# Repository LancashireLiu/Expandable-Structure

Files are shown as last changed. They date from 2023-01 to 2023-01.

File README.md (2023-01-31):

# 可展多面体机构

这个项目是未来技术学院本科二年级设计与建造Ⅱ课程的课程设计，我是本项目的组长。下面Readme文档简要介绍了本项目的过程，上方repository库中包含了项目的全过程以及报告等内容！

天津大学可动结构实验室的马家耀教授[个人主页](http://motionstructures.tju.edu.cn/ch/team/majiayao.html)为本项目的导师。

***

可展多面体机构是一种在实现其承载功能的前提下，能够大尺寸地改变几何形状与空间构型的结构。

可展多面积机构可以适应不同的应用需求，是空间可折展结构和大型可折展设备的关键技术。

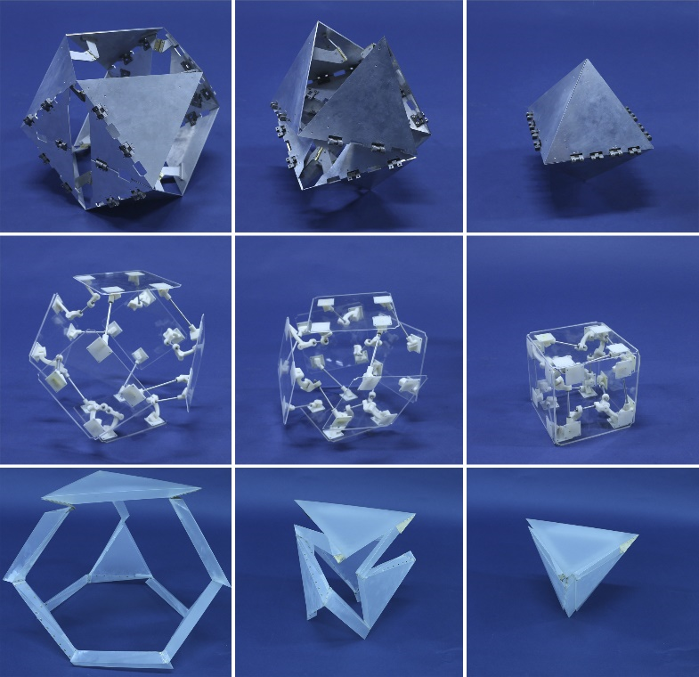
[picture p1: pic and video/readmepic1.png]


单自由度可展多面体机构可以实现单一驱动下两个空间构型的切换，如上图中截角八面体和立方体之间的变换，在展开时可大幅增加工作空间与面积，在完全折叠状态下可减少储存和运输空间。对多面体展开与折叠构型进行分析，确定各顶点的运动副类型及方位，用以形成具有协调运动的多面体空间机构网格。

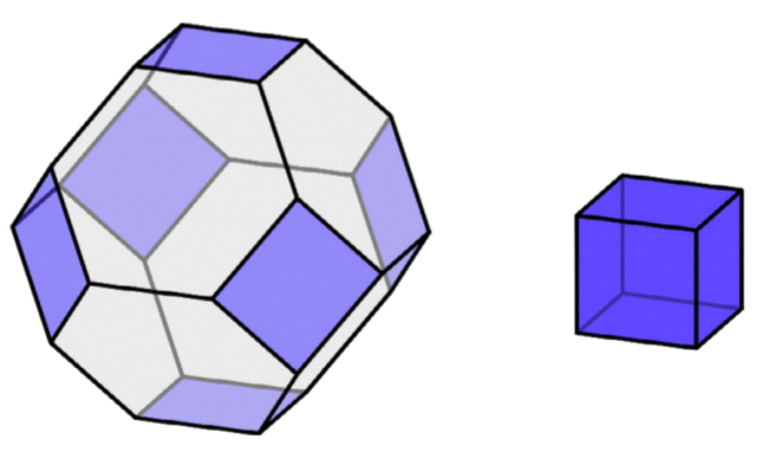
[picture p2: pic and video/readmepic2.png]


上图中中层的截角八面体和立方体之间的可展结构就是我们的项目。

为了保证机构在空间中运动是保持单自由度的，多面体每个连杆和正方形表面之间的连接转轴（称为转动副）需要是确定的。这种连杆机构称为Bricard机构，通过空间几何性质可以计算出这些转轴（转动副）和完全活动的顶点（称为球副）的空间坐标和角度。

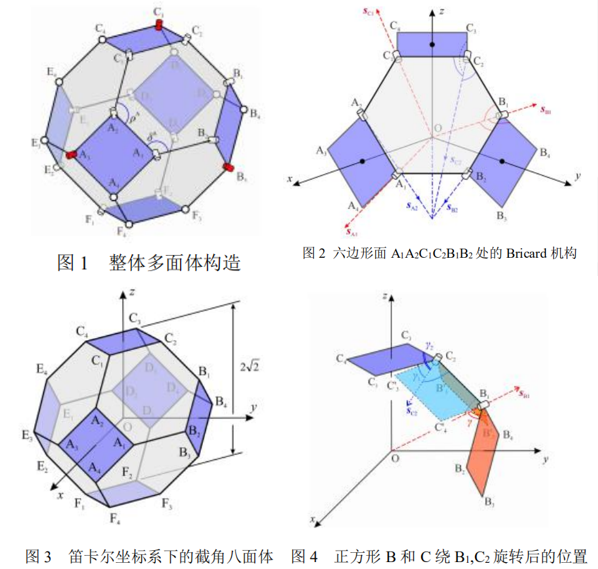
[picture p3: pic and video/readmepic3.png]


> 机构初始状态为一截角八面体，其整体构造如图 1 所示。本机构以三重对称 Bricard 连杆机构为折展运动单元，采用 15 个转动副与 9 个球副。经计算，该可 展机构的自由度为 1。Bricard 机构如图 2 所示。原点的定义及坐标系的建立如图 3 所示。正方形 B 围绕 B1 关节轴线旋转，正方形 C 围绕 C2关节旋转，使 B4与 C2重合，C1 与 B1 重合（如图 4 所示），由于 Bricard 机构的三重对称性以及六 边形 D1D2E1E2F1F2与六边形A1A2C1C2B1B2结构相同，因此可得出其他点的运动 过程。其运动顺序如图 4 所示。

可展机构

通过立体几何矩阵理论可以计算出所有结点在空间中的位置和转轴（转动副）的朝向向量。

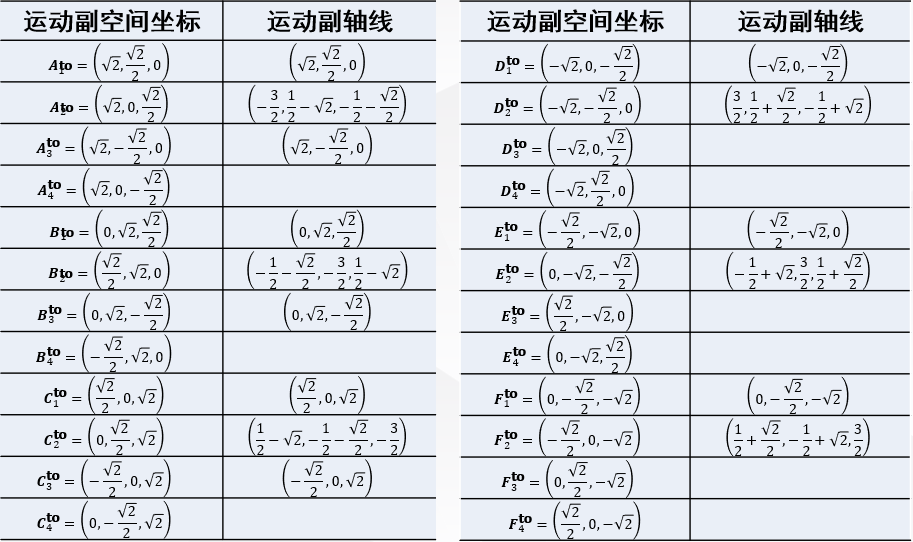
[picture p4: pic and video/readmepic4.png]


之后用Solidworks进行建模，首先建立三个面的Bricard结构，然后用两个相同的Bricard结构拼接成最后的模型。

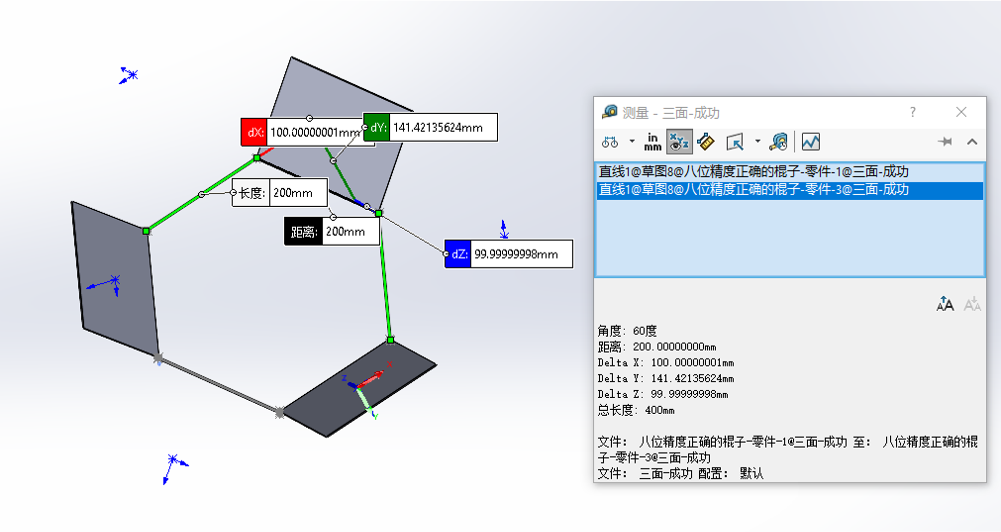
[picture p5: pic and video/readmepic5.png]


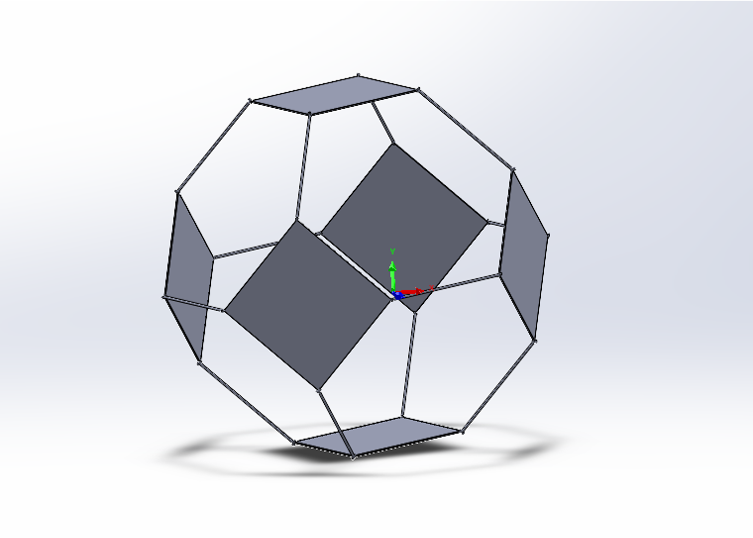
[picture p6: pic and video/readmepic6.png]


[运动学建模视频](https://github.com/LancashireLiu/Expandable-Structure/blob/main/pic%20and%20video/video1.mp4)

进行零件、静态和动力学建模后，我确定了实物大小，实物材料（表面使用亚克力板，转动副和球副3d打印，连杆不锈钢），使用建模出的数据打印和制作，拼装后得到实物。

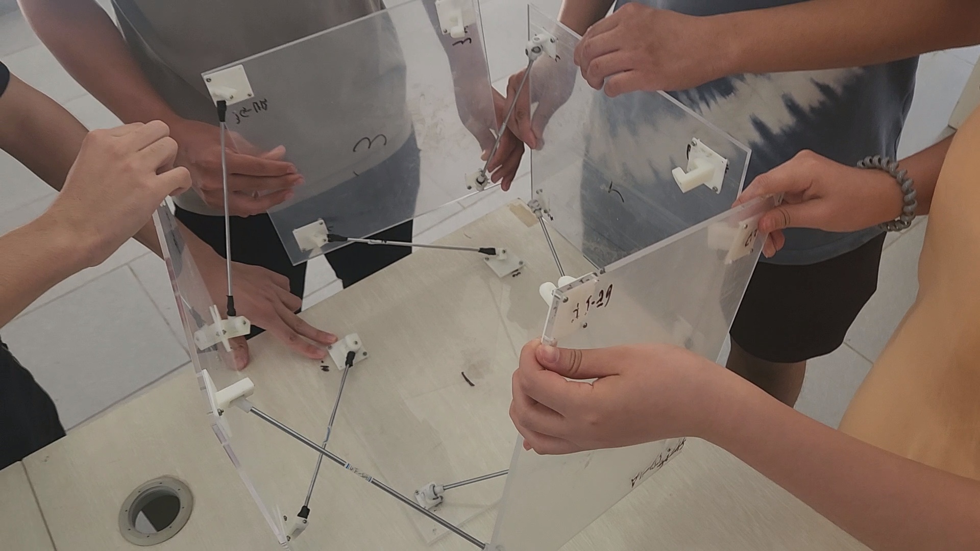
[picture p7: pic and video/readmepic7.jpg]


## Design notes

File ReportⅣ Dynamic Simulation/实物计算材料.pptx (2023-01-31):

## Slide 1

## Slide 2

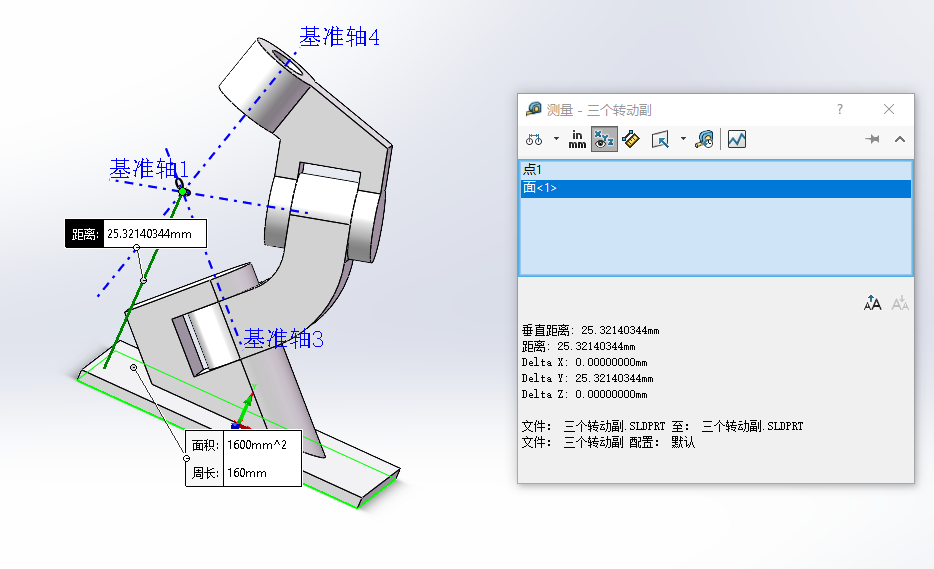
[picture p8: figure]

- H=2.53cm

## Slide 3

可展结构——运动学仿真分析

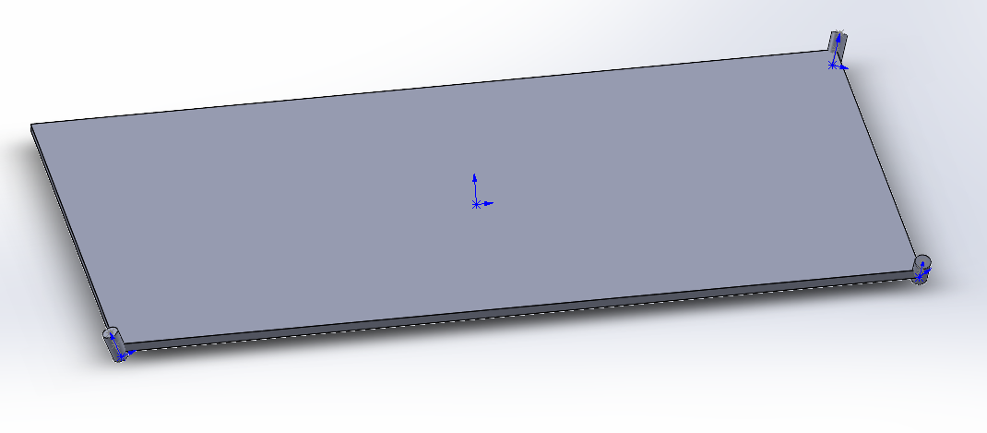
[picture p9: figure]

Ⅱ类转动副
与C1C4、C1C2夹角：108.43494882°、 108.43494882°

C3

C4

C2

C1

Ⅱ类转动副
与C2C1、C2C3夹角： 95.57617619°
134.72950752°

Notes: 两个转动副扭角：34.78648675°，和连杆的情况一样，接下来只需要拼接即可

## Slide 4

- 转动副Ⅰ
- h=1.98cm

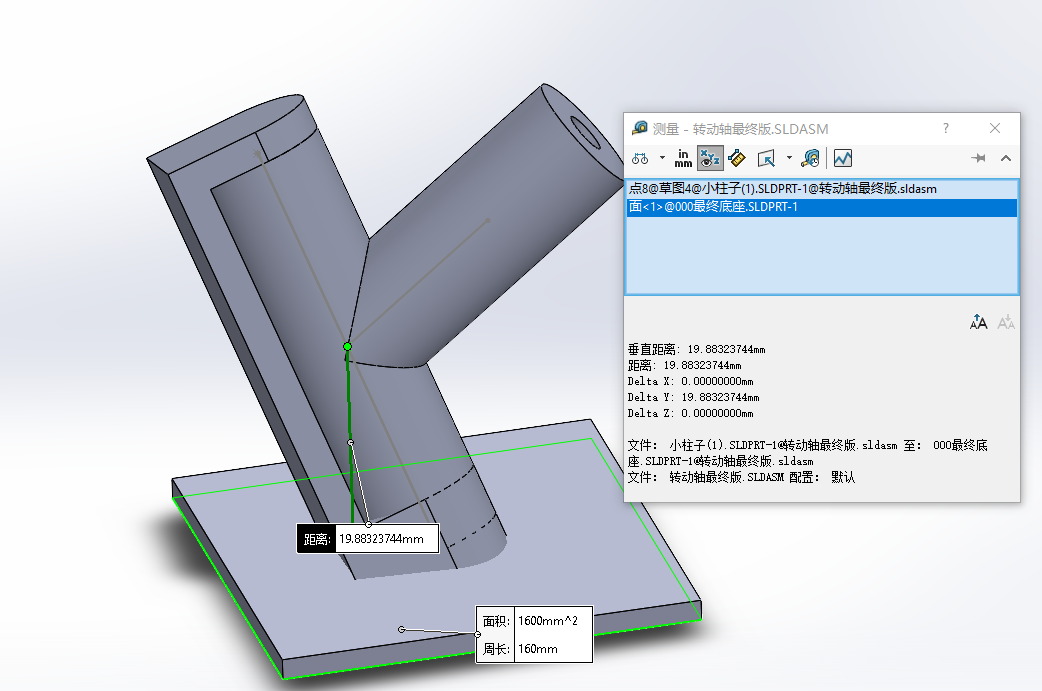
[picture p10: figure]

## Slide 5

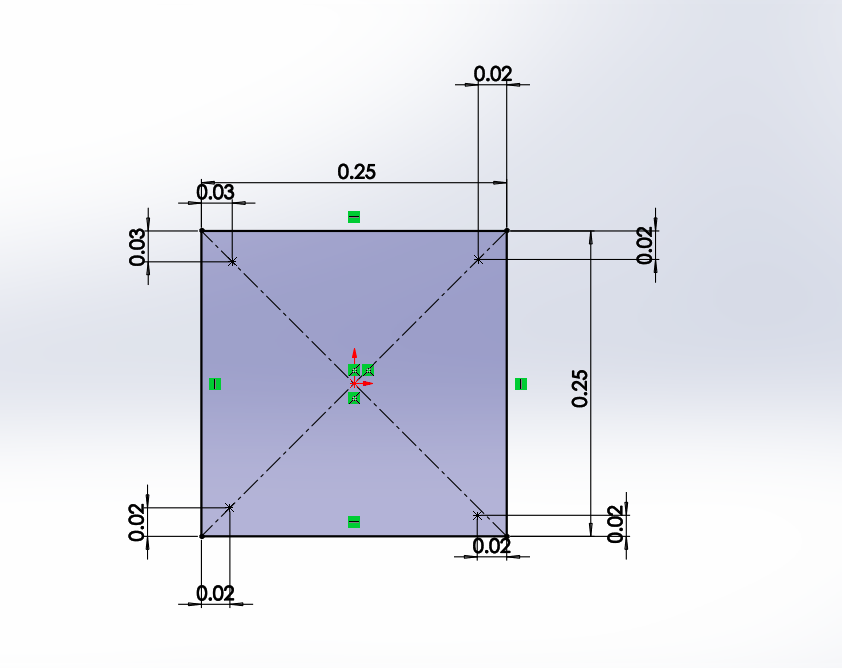
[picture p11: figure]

2.53cm

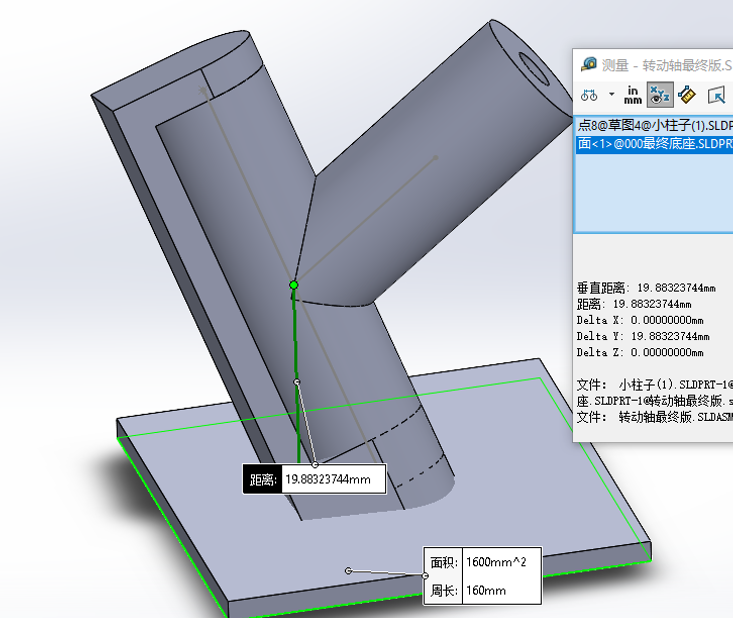
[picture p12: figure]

2.34cm

1.73cm

2.34cm

2.42cm

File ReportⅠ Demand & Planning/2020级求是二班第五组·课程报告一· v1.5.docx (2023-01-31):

课程报告1 项目计划

1.1 可展结构资料综述

可展机构在航空航天、建筑、汽车、消防等领域都有着广泛的应用，是人类用以传递力的重要机构。随着全球工业化的快速发展，机械基本上取代了传统的手工的发展，而可展机构为人类生活生产提供了不可忽视的便利性，在航天航空、日常生活, 机器人等领域应用广泛。因此这种机构的机械设计和运动分析研究得到国内研究机构的普遍重视。但对于不同可展机构的开发与应用, 还需要更多针对性的研究与探索。

可展结构的具有众多优秀特性。

（1）结构紧凑、尺寸小巧，且设备收缩后体积小。这是可展机构最大的优点，也使得其作业所要求的占用空间小。在地下水位较高的地区工作时对机坑的处理会十分简单。它能够在任何已有设备上直接使用，而无需修改设备结构和机坑深度。

（2）载荷能力大、稳定性好。相对于其他机构来讲，大部分可展机构的承载能力偏大。由于其稳定的结构，可展机构在额定承载能力和伸展长度下，具有很好的稳定性。

（3）定位精准。大部分可展机构在运行过程能确保在行程的任意一点精确定位，并锁定高度，不像液压设备会因温度的变化或泄漏产生位置变化。

（4）运行平稳、噪音较低。由于其连续成型原理，无垂直方向爬行，使得机构运转平稳安静，除驱动装置的运行噪音，大部分可展器本身的工作噪音很低。

（5）效率高。大部分可展设备的总传动效率较高，通常可达到 80%以上。

（6）构造简单，使用方便。可展机构的结构精巧而简洁，所以可展器本身的安装工作简易而快捷，一块伸缩机构通常在很短的时间即可安装使用。

（7）通用性高。可展机构对使用环境没有太高要求，使其经常在太空、海洋等复杂环境下工作，并依然保持其稳定性。

我们所需要的完成的截角八面体 (由八个六边形和六个四边形围成的十四面体)的体积折展比分别为11.3，可在展开状态下可显著提升工作空间。这些多面体变换过程无运动分叉现象, 具有结构简单和易于控制等特点。通过桁架变换方法，构件可在保持单自由度变换特点的同时降低机构的过约束度数, 从而以较低过约束度甚至非过约束的机构实现变换，减少因过约束带来的制造和装配的苛刻要求，也避免了因构件变形而产生的机构锁死现象，增强了应用的可行性。

1.2 工程师职责

（1）注重产品质量，控制好产品研发进度。

（2）协调各方面工作，确保工作顺利进行。

（3）每周完成组内分配的任务，认真执行计划，按时汇报自己的工作，不因为个人原因拖慢组内进度。

（4）端正工作态度，严谨认真，刻苦钻研，脚踏实地，讲求效率。

（5）正确认识自我，遇到问题及早提出。

1.3 项目管理

项目进度安排甘特图如图1-1 。

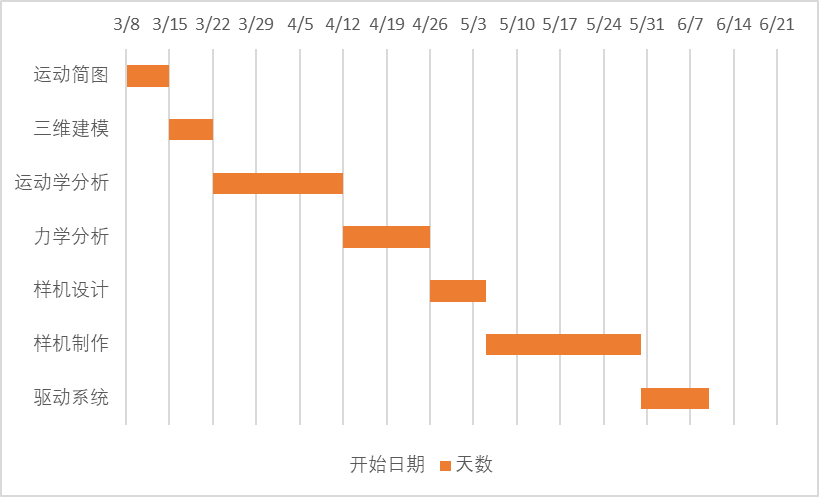
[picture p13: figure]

图1-1 项目进度安排甘特图

成员分工安排如下：

刘宇轩：组长，负责主管项目进程，组员的任务分配及监督各项任务的完成情况。在具体工作上，负责可展多面体运动简图的描画，三维建模过程，运动学过程分析，力学过程分析，样机设计及制作。

张佳瑜：负责可展多面体运动简图的描画，运动学过程分析，力学过程分析，样机设计及制作。

罗松寒：负责可展多面体运动简图的描画，三维建模过程，运动学过程分析，力学过程分析，样机制作。

白韬：负责可展多面体运动简图的描画，运动学过程分析，力学过程分析，样机制作，可展多面体驱动系统，。

郭伟祺：负责可展多面体运动简图的描画，三维建模过程，运动学过程分析，力学过程分析，样机制作。

冒惠敏：负责可展多面体运动简图的描画，运动学过程分析，力学过程分析，样机设计与制作。

1.4 项目任务书

项目题目——可展机构

1.4.1 用途及功能要求

可展多面体机构在实现其承载功能的前提下，能够大尺寸地改变几何形状与空间构型，以适应不同的应用需求，是空间可折展结构和大型可折展设备的关键技术。单自由度可展多面体机构可以实现单一驱动下两个空间构型的切换，如图一中截角八面体和立方体之间的变换，在展开时可大幅增加工作空间与面积，在完全折叠状态下可减少储存和运输空间。对多面体展开与折叠构型进行分析，确定各顶点的运动副类型及方位，用以形成具有协调运动的多面体空间机构网格。图1-2展示了截角八面体和立方体之间的变换。


图1-2 截角八面体和立方体之间的变换

1.4.2 设计要求和原始数据

（1）设计一种可在截角八面体与立方体之间变换的可展多面体机构；

（2）可展多面体折叠构型下立方体边长200-300mm，机构自由度≤2；

（3）可展多面体折展过程中需避免因零件碰撞而产生的物理干涉；

（4）可展多面体在完全展开状态需保证构型的稳定性。

设计原始数据如下：

表1-1 设计原始数据

方 案 号 | 1－1 | 1－2 | 1－3 | 1－4
整体自由度数 | 1 | 2 | 1 | 2
折叠构型下立方体边长a/mm | 200 | 200 | 300 | 300

1.4.3 设计内容

（1）确定可展多面体折展前后的顶点坐标及多边形单元的基本尺寸；

（2）选定可展多面体顶点处运动副形式，计算转动副空间轴线位置，设计转动副的物理实现形式；

（3）设计合理的零件外形及具体尺寸并确定各类零件数量，避免物理干涉；

（4）设计锁死装置保证可展多面体具有稳定展开构型。

1.4.4 提交的设计结果

（1）可展多面体的机构运动简图，包括顶点处运动副类型，以及转动副空间方位；

（2）可展多面体三维软件建模模型，需包含运动模拟中的3-4个典型折展状态；

（3）可展多面体典型顶点运动轨迹；

（4）可展多面体静力学分析；

（5）各类零件尺寸图若干张；

（6）原理样机；

（7）设计计算说明书，内容包括：

* 设计流程和设计原始数据；

* 可展多面体顶点坐标与各个顶点处转动副的具体轴线方位计算；

* 可展多面体三维建模的过程说明；

* 零件外形及具体尺寸的设计文本。

1.4.5 评价指标及标准

（1）尺寸小、自由度少、体积折展大；

（2）原理样机具有较为规则平整的外观构型；

（3）原理样机能够在最大与最小构型之间折展，且折展过程流畅；

（4）原理样机在完全展开状态应具有较高的稳定性和承载力。

1.5 项目需求分析

表1-2展示了可展多面体的项目需求分析。

表1-2 项目需求分析

需求分析 | 需求表达
机构设计需求 | ① 可展机构 ② 结构体系 ③ 驱动源
用户情况 | 1 面向用户对象 2 使用场合、领域
作品效益 | 1 社会效益及经济效益 2 时间消耗及产出 3 使用频率 4 资金消耗及回报 5 信息使用价值

1.6 产品规格

1.产品体积：可展多面体折叠构型下立方体边长200-300mm，体积大小为8000cm³-27000cm³。

2.产品结构：本机构以三重对称 Bricard 连杆机构为折展运动单元，采用 15 个转动副与 9 个球副。

3.自由度：机构自由度≤2。

4.驱动源:

（1）微电机驱动

在结构上分散或集中布置微电机，直接驱动主动件或通过传动使机构展开或折叠。

（2）弹簧(扭簧、拉簧)元件驱动

在机构节点或杆件中点处按特定要求设詈弹簧元件，折叠时弹簧受预应力存贮弹性变性能；当机构解锁后，弹簧释放弹性能，驱动机构协调同步展开。

（3）自伸展驱动

结构的一部分构件、某些特定构件的中点、整个结构元件，由记忆合金、自适应智能元件等构成，使其在特定环境下可按设计要求自动展开。

5.自锁方式:

（1）有限自锁

在摇杆末端设置一个小凹槽，凹槽位置在转动结束后所在的角度上。在固定 处固定一个细短杆，转动结束后细短杆刚好接到凹槽里。或者在两面之间添加一 个伸缩杆，伸缩杆通过类似装置实现自锁（类比雨伞），从而实现两面高度之间的自锁。

优点：旋转结束后，自锁较稳定。

缺点：回复原六面体有不确定因素。

（2）棘轮自锁

在某一转动副处进行改装，安装一个棘轮。保证转动副只按照特定轨迹单向转动，从而保证在展开的各个阶段都能得到较好的稳定性。此外通过对棘轮的解放，实现由截角八面体到六面体的转换。或者在两个面之间安装连杆装置，通过棘轮实现自锁。

优点：稳定度高，不确定因素少。

缺点：装置复杂，制作过程困难。

（3）涡轮涡杆自锁

在两面之间安装涡轮涡杆结构，通过设计螺旋角和摩擦系数实现自锁。

优点：稳定度高，不确定因素少。

缺点：计算量大，装置复杂。

表1.3展示了项目作品的规格参数表。

表1.3 产品规格参数表

产品规格参数表
产品构件组成 | 零件类型 | 方形面板 | 铰链底座 | 直杆1 | 直杆2 | 直杆3
| 数量(个） | 6 | 24 | 6 | 6 | 3
| 零件类型 | 弯杆1 | 弯杆2 | 螺栓 | 轴承 | 圆柱销
| 数量（个） | 9 | 9 | 96 | 18 | 30
产品数据参数 | 立方体边长 | 自由度 | 驱动源 | 自锁方式 | 折展比 | 折展解构单元
| 280mm | 1 | 微电机 | 棘轮自锁 | 11.314 | 三重对称Bricard连杆机构

1.7 产品概念选择

六步骤选择项目作品概念

步骤一：准备选择矩阵

作品概念评分矩阵表如表1.4

表1.4 概念评分矩阵表

作品概念
选择标准 | 权重 | 自锁方式 | | | | | | 驱动方式
| | 有限自锁 | | 棘轮自锁 | | 涡轮涡杆自锁 | | 微电机驱动 | | 弹簧驱动
| | 评分 | 加权分 | 评分 | 加权分 | 评分 | 加权分 | 评分 | 加权分 | 评分 | 加权分
精确度 | 25% | 3 | 0.075 | 4 | 0.1 | 4 | 0.1 | 4 | 0.1 | 3 | 0.075
稳定性 | 20% | 4 | 0.08 | 5 | 0.1 | 4 | 0.08 | 4 | 0.08 | 3 | 0.06
流畅度 | 15% | 4 | 0.06 | 4 | 0.06 | 5 | 0.075 | 4 | 0.06 | 3 | 0.045
可恢复性 | 10% | 2 | 0.02 | 4 | 0.04 | 4 | 0.04 | 3 | 0.03 | 1 | 0.01
资金预算 | 10% | 5 | 0.05 | 3 | 0.03 | 2 | 0.02 | 2 | 0.02 | 3 | 0.03
计算量 | 10% | 3 | 0.03 | 4 | 0.04 | 2 | 0.02 | 2 | 0.02 | 2 | 0.02
组装难易 | 5% | 4 | 0.02 | 2 | 0.01 | 3 | 0.03 | 2 | 0.01 | 2 | 0.01
整体重量 | 5% | 5 | 0.025 | 4 | 0.02 | 3 | 0.015 | 2 | 0.01 | 4 | 0.02
总评 | 100% | 0.36 | | 0.4 | | 0.38 | | 0.33 | | 0.27
是否采用 | | 否 | | 是 | | 否 | | 是 | | 否

步骤二：作品概念评估

以所有标准，对一个概念评估，然后转向下一个概念。

选择标准：精确度、稳定性、流畅度、可恢复性、资金预算、计算量、组装难易、整体重量。

步骤三：作品概念排序

自锁方式：1.棘轮自锁 2.涡轮涡杆自锁 3.有限自锁

驱动方式：1.微电机驱动 2.弹簧驱动

步骤四：作品概念组合与改进

对作品概念进行组合，保持优势，减少劣势。

步骤五：选出一个作品概念

选择结果：棘轮自锁、微电机驱动

步骤六：反思结果与过程

检查选出的作品概念，确保每位成员满意。

1.8 产品目标指标

1.尺寸：可展多面体折叠构型下立方体边长280mm。

2.自由度：可展机构的自由度为1。

3.驱动源：经过项目作品概念评估矩阵表加权之后权重最高的驱动方式，经评定为微电机驱动的方式。

4.自锁方式：经过项目作品概念评估矩阵表加权之后权重最高的自锁方式，经评定为棘轮自锁的方式。

表1.5展示了项目作品的最终指标。

表1.5 产品最终指标

选择标准 | 指标要求
精确度 | 自锁角度误差小于3%
稳定性 | 展开结构承重极限≥500g
流畅度 | 响应时间≤0.1秒
可恢复性 | 恢复时间≤3秒
产品大小 | 立方体边长≤280mm

1.9 运动副坐标及轴线计算结果

表1.6展示了可展多面体的运动副和运动副轴线的计算结果。详细的计算过程在本报告附件1可展多面体-设计计算说明书中展示。

表1.6 计算结果

运动副空间坐标 | 运动副轴线
A_1^(to) =(√2,(√2)/2,0) | (√2,(√2)/2,0)
A_2^(to) =(√2,0,(√2)/2) | (-3/2,1/2-√2,-1/2-(√2)/2)
A_3^(to) =(√2,-(√2)/2,0) | (√2,-(√2)/2,0)
A_4^(to) =(√2,0,-(√2)/2)
B_1^(to) =(0,√2,(√2)/2) | (0,√2,(√2)/2)
B_2^(to) =((√2)/2,√2,0) | (-1/2-(√2)/2,-3/2,1/2-√2)
B_3^(to) =(0,√2,-(√2)/2) | (0,√2,-(√2)/2)
B_4^(to) =(-(√2)/2,√2,0)
C_1^(to) =((√2)/2,0,√2) | ((√2)/2,0,√2)
C_2^(to) =(0,(√2)/2,√2) | (1/2-√2,-1/2-(√2)/2,-3/2)
C_3^(to) =(-(√2)/2,0,√2) | (-(√2)/2,0,√2)
C_4^(to) =(0,-(√2)/2,√2)
D_1^(to) =(-√2,0,-(√2)/2) | (-√2,0,-(√2)/2)
D_2^(to) =(-√2,-(√2)/2,0) | (3/2,1/2+(√2)/2,-1/2+√2)
D_3^(to) =(-√2,0,(√2)/2)
D_4^(to) =(-√2,(√2)/2,0)
E_1^(to) =(-(√2)/2,-√2,0) | (-(√2)/2,-√2,0)
E_2^(to) =(0,-√2,-(√2)/2) | (-1/2+√2,3/2,1/2+(√2)/2)
E_3^(to) =((√2)/2,-√2,0)
E_4^(to) =(0,-√2,(√2)/2)
F_1^(to) =(0,-(√2)/2,-√2) | (0,-(√2)/2,-√2)
F_2^(to) =(-(√2)/2,0,-√2) | (1/2+(√2)/2,-1/2+√2,3/2)
F_3^(to) =(0,(√2)/2,-√2)
F_4^(to) =((√2)/2,0,-√2)

1.10 设计草图

图1-3、1-4、1-5、1-6、1-7、1-8展示了本组成员绘制的设计草图。

刘宇轩：

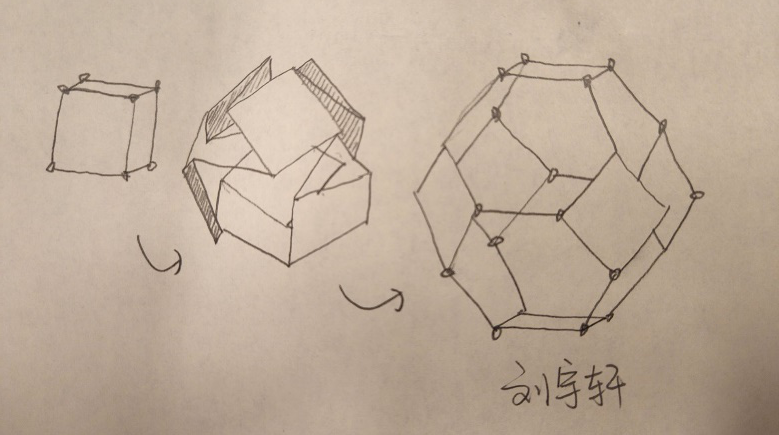
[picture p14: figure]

图1-3 刘宇轩设计草图

张佳瑜：

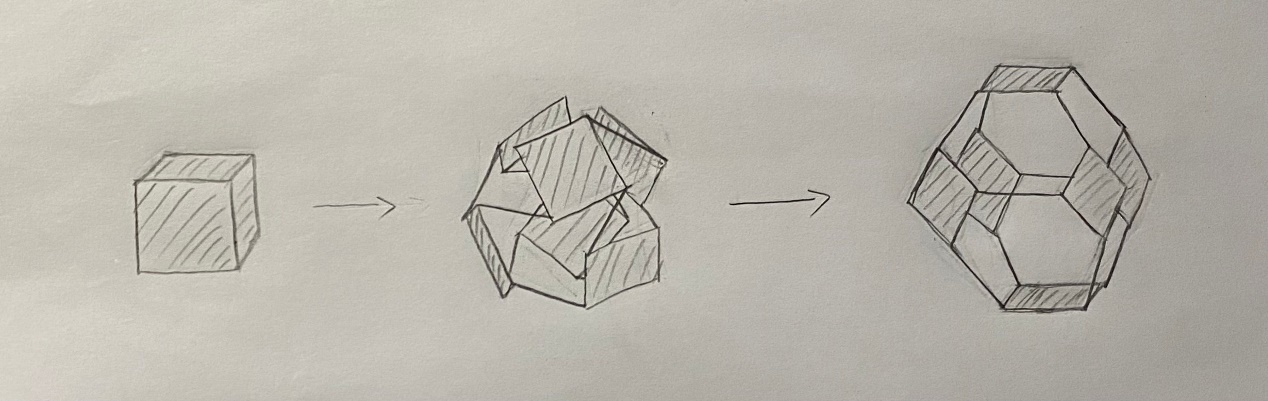
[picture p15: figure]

图1-4 张佳瑜设计草图

罗松寒：

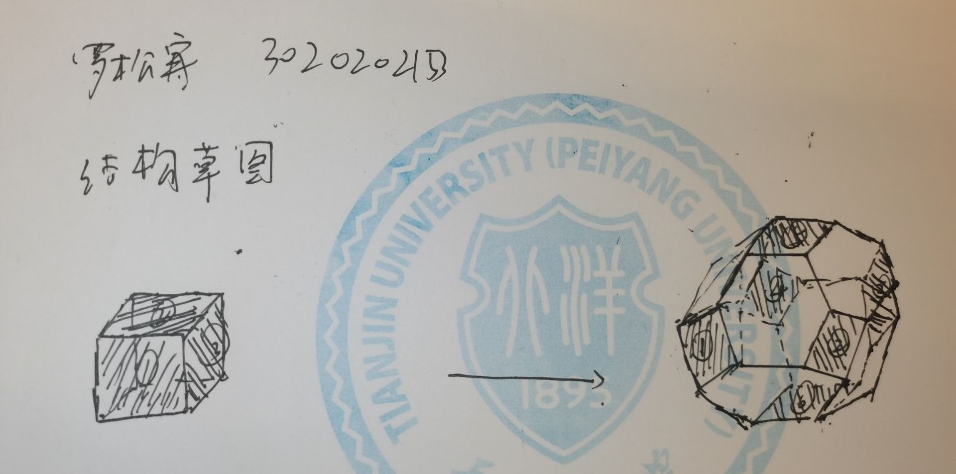
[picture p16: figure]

图1-5 罗松寒设计草图

白韬：

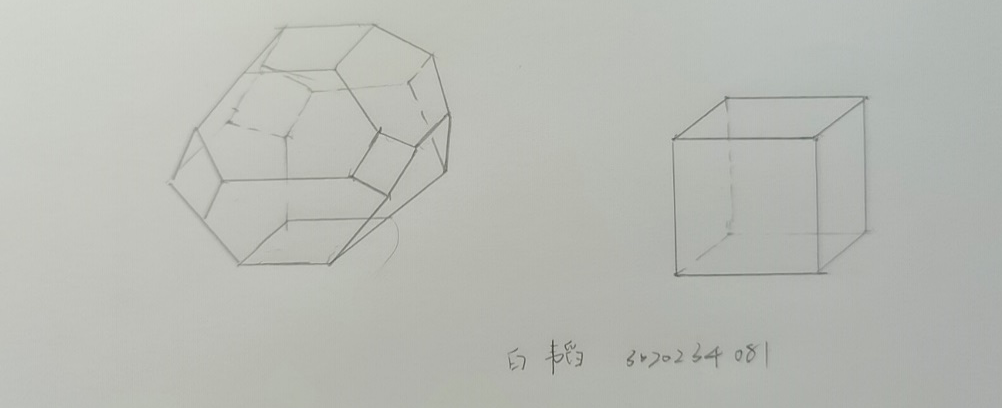
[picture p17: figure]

图1-6 白韬设计草图

郭伟祺：

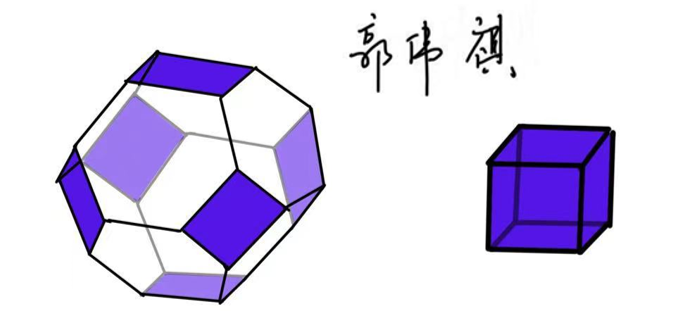
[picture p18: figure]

图1-7 郭伟祺设计草图

冒惠敏：

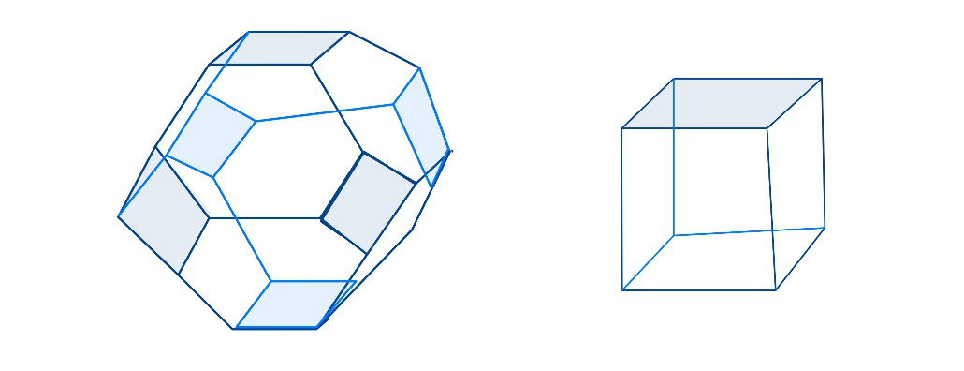
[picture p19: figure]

图1-8 冒惠敏设计草图

1.11 任务情况完成小结

本周期小组主要完成了初期项目的准备和管理工作并安排下一阶段的任务，进行各运动副的空间坐标和轴线方向计算并初步确定项目的关键节点确定和时间分配。下面展示了各成员的任务完成情况小结。

刘宇轩：进行组员分工并划分任务，进行会议记录；负责项目综述和项目安排部分的研讨课展示；负责可展多面体的计算工作；负责课程报告一的合稿整理。

张佳瑜：负责需求分析应用领域部分的研讨课展示；负责产品课程报告产品概念内容。

罗松寒：负责需求调查产品实现部分的研讨课展示；负责产品课程报告任务书、项目管理内容。

白韬：负责项目背景部分的研讨课展示；负责产品课程报告产品综述内容。

郭伟祺：负责需求调查产品应用场景与服务对象部分的研讨课展示；负责产品课程报告甘特图、需求表达部分内容。

冒惠敏：负责需求分析产品实现部分的研讨课展示；负责产品课程报告产品规格、目标指标、产品参数部分内容。

设计与建造 课程小组会议记录

议题 | | 项目前期准备讨论会
组长 | | 刘宇轩 | 年级/班级/组别 | | | 2020级 2 班 第 5 组
组员 | | 郭伟祺 白韬 冒惠敏 罗松寒 张佳瑜
会议时间 | 2022年3月9日 | | | 会议地点 | 郑东图书馆306研究厢
讨论内容 | 会议围绕初期的项目准备以及任务分配问题展开，主要讨论并解决了以下内容。 1.讨论了项目任务工作的分配。 2.安排前期调研和第一次课程报告任务，以及计算可展多面体顶点和运动副的空间坐标。 3.确定项目管理与时间规划，评估并分配各个项目的时间并制作甘特图。
下一步工作计划 | 1.完成可展多面体的设计计算 2.使用solidworks对项目多面体进行建模。
附件材料清单

附件1：可展多面体-设计计算说明书

理论计算部分

1 体积折展比

设计方案选择截角八面体和立方体之间的变换，设正多边形边长为a, 截角八面体体积为 8√2a^3 ，立方体体积为 a^3 ，则理论体积折展比为 8√2≈11.314 。

2 两种构型下各顶点坐标

如图1.9所示，在截角八面体中，每个六边形面（如 A_1 A_2 C_1 C_2 B_1 B_2 ）被三个正方形面和三个连接杆包围，呈现出三重对称性。如果把这些六边形的白色面折叠起来，剩下的六个正方形蓝色面就会形成一个立方体。因此，我们将从三重对称Bircard机构开始构造具有多环连杆的多面体变换方案。

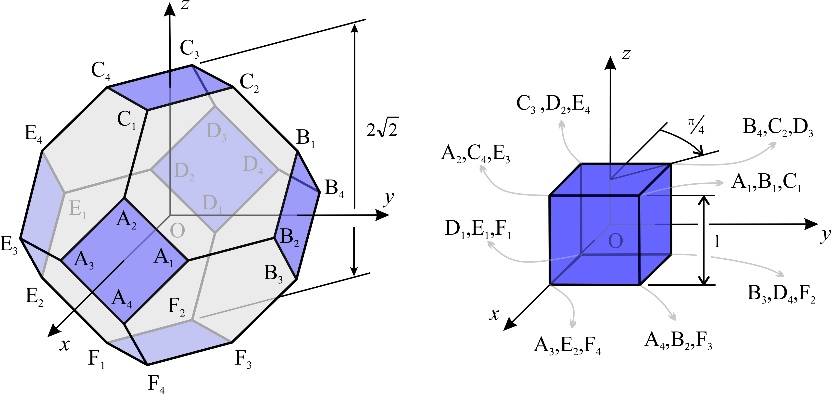
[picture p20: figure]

图1.9 截角八面体和立方体之间的变换

一个截角八面体和一个具有单位长度边的立方体，如果在变换期间没有发生干涉，则其顶点运动前后的坐标是唯一的，并且所有的八个六边形空洞将在转变后消失。使用图1.9中所示的笛卡尔坐标系，通过顶点的位置可以更好地说明多面体之间的转换。

当多面体的每边都有单位长度时，截角八面体所有24个顶点坐标为：（其中上角标“to”表示截角八面体—truncated octahedron。）

A_1^(to) =(√2,(√2)/2,0)

A_2^(to) =(√2,0,(√2)/2)

A_3^(to) =(√2,-(√2)/2,0)

A_4^(to) =(√2,0,-(√2)/2)

B_1^(to) =(0,√2,(√2)/2)

B_2^(to) =((√2)/2,√2,0)

B_3^(to) =(0,√2,(√2)/2)

B_4^(to) =(-(√2)/2,√2,0)

C_1^(to) =((√2)/2,0,√2)

C_2^(to) =(0,(√2)/2,√2)

C_3^(to) =(-(√2)/2,0,√2)

C_4^(to) =(0,-(√2)/2,√2)

D_1^(to) =(-√2,0,-(√2)/2)

D_2^(to) =(-√2,-(√2)/2,0)

D_3^(to) =(-√2,0,(√2)/2)

D_4^(to) =(-√2,(√2)/2,0)

E_1^(to) =(-(√2)/2,-√2,0)

E_2^(to) =(0,-√2,-(√2)/2)

E_3^(to) =((√2)/2,-√2,0)

E_4^(to) =(0,-√2,(√2)/2)

F_1^(to) =(0,-(√2)/2,-√2)

F_2^(to) =(-(√2)/2,0,-√2)

F_3^(to) =(0,(√2)/2,-√2)

F_4^(to) =((√2)/2,0,-√2)

3 Bricard机构的配置

首先，让我们从六边形面 A_1 A_2 C_1 C_2 B_1 B_2 开始配置Bricard机构。如图1.10所示，它的初始形状是一个正六边形，变换后，顶点 A_1 , C_1 , B_1 收敛到立方体上的一个顶点（如图1.9右图所示）。因此，该六边形面的运动将具有三重对称性。在这些顶点配置转动关节后，为了实现预期运动，所形成的折展运动单元必须是三重对称Bricard连杆机构。

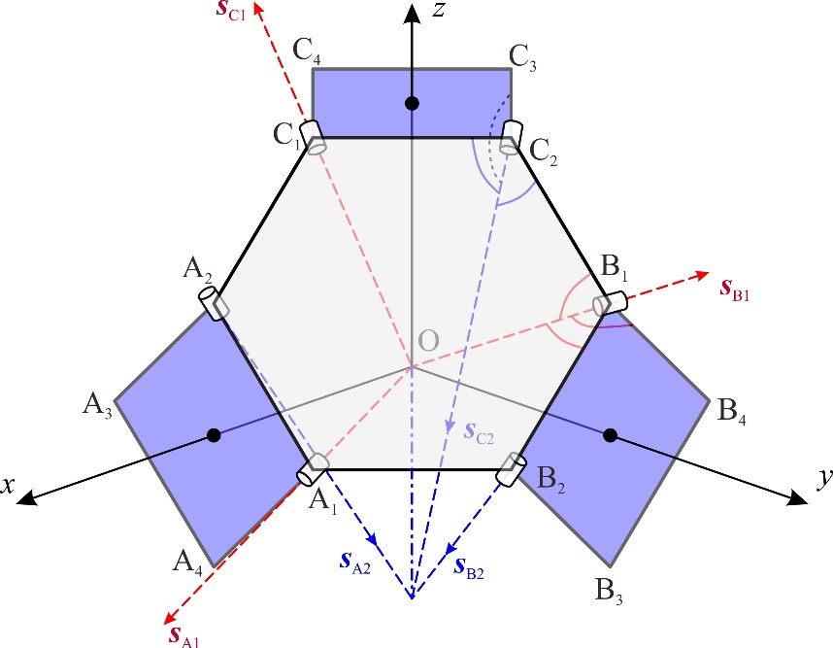
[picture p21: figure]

图1.10 六边形面 A_1 A_2 C_1 C_2 B_1 B_2 处的Bricard机构

图1.11显示了截角八面体的正方形B和C，以及在坐标系中固定B1C2时它们的最终位置。当正方形B围绕 B1关节轴线旋转时，顶点 B4 转到 C2，可得到 B_4^(') =C_2^(to) =TB_4^(to) 和 B_1^(') =TB_1^(to) ，则3×3变换矩阵T为：

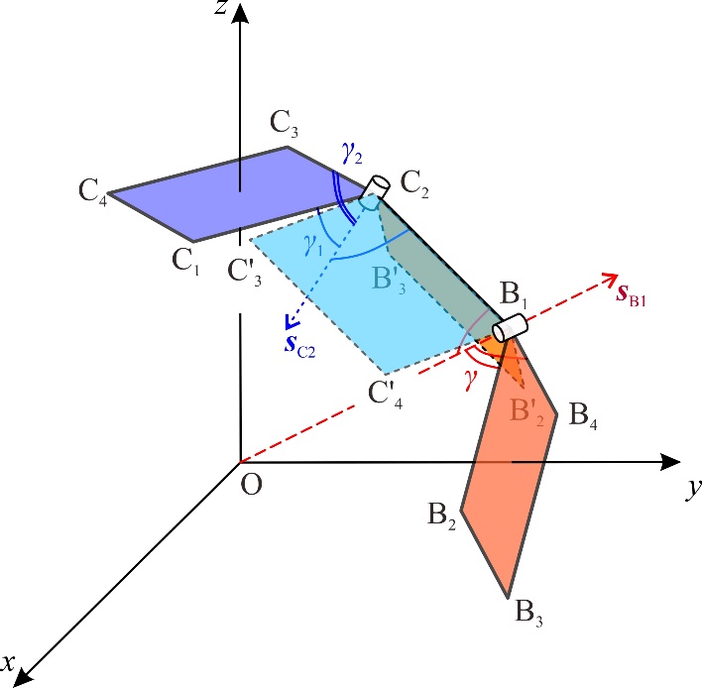
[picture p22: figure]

图1.11 正方形B和C绕 B1 ,C2绕旋转后的最终位置

T=[-2/3, -1/3, 2/31/3, 2/3, 2/3-2/3, 2/3, -1/3]

利用T进而求得 B_2^(') 的位置为

B_2^(') =TB_2^(to) = (-2/3√2,5/6√2,1/3√2)

最终位置的正方形B和C形成立方体的两个垂直面，于是有

B_1^(to) C_4^(') =B_1^(to) C_2^(to) ×B_1^(to) B_2^(') _2

则 C_4^(') 的最终位置为

C_4^(') =(1/3,-2/3+√2,(√2)/2-2/3)

正方形C沿着 C2处转动关节做整体刚性转动，所以轴线位置 s_(C2) 为 C_1^(to) C_1^(') 和 C_4^(to) C_4^(') 公垂线方向，则可得到

s_(C2) =(1/2-√2,-1/2-(√2)/2,-3/2)

由于Bricard机构的三重对称性，如图1.9中坐标系所示，假设六边形面 A_1 A_2 C_1 C_2 B_1 B_2 处的机构绕向量 (1, 1, 1)^T （六边形面法线方向）整体旋转120°，则 s_(B1) 转到 s_(C1) ， s_(C1) 转到 s_(A1) ，那么有 s_(C1) =T_1 s_(B1) 和 s_(A1) =T_1 s_(C1) ，此变换矩阵T1为

T_1 =[0, 0, 11, 0, 00, 1, 0]

利用同样的120°旋转变换， s_(C2) 则转到 s_(A2) ， s_(A2) 转到 s_(B2) ，就可得到A2 和B2处转动副轴线方向

s_(A2) =T_1 s_(C2) =(-3/2,1/2-√2,-1/2-(√2)/2)

s_(B2) =T_1 s_(A2) =(-1/2-(√2)/2,-3/2,1/2-√2)

由于图1.9中六边形D1D2E1E2F1F2与A1A2C1C2B1B2不直接连接，且这两个六边形的结构是相同的，因此在六角边形D1D2E1E2F1F2设置相同的Bricard机构。利用三维对称性，2个六边形处的Bricard机构关于坐标原点对称，其中 s_(D1) ,s_(E1) ,s_(F1) 依然相交于坐标原点并分别指向各自对应顶点，则其各个顶点处转动关节的轴线可按照上述求解过程同理可得：

s_(D1) =(-√2,0,-(√2)/2)

s_(D2) =(3/2,1/2+(√2)/2,-1/2+√2)

s_(E1) =(-(√2)/2,-√2,0)

4 整体系统的机构网格

到目前为止，为构造多面体连杆机构，已经求得两个相同的三重对称Bricard机构的转动轴线位置，如图1.12所示，除Bricard机构所含的转动关节（12个），其余顶点则暂时设置为球副。计算机模拟后，此可折展多面体具有两个自由度。进一步的，利用对称性，将A3 , B3 和C3处的球副替换转动副，可得到单自由度系统。

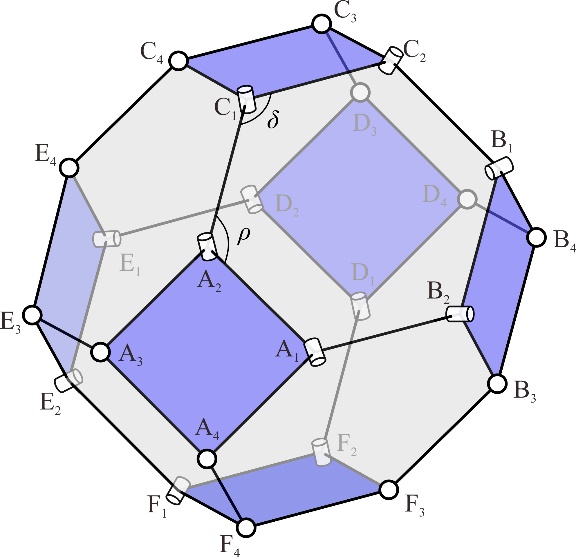
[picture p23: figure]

图1.12 包含两个Bricard机构的整体多面体构造

其中，与B1的轴线方位相似，A3处转动关节可平分∠A2A3E3并指向多面体中心，则杆A2A3与杆E3A3绕其转动后可重合。同理，A3，B3，C3处转动关节相交于坐标原点并分别指向各自对应顶点，则有

s_(A3) =(√2,-(√2)/2,0)

s_(B3) =(0,√2,-(√2)/2)

s_(C3) =(-(√2)/2,0,√2)

课程报告2 三维建模

2.1 产品零件的确定与连接方式选择

2.1.1 零件形状及尺寸

(1)连接板

下图展示了Bricard机构中关键连接板的具体设计尺寸。

如图2-1所示，该连接板长、宽均为200mm，厚3mm的正方形板，并在四角处切掉了长为5mm的等腰直角三角形，以防止在展开时可能发生的机构干涉现象。

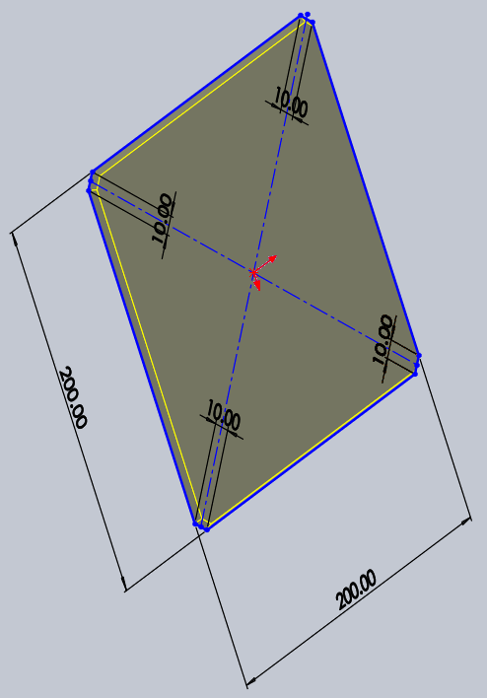
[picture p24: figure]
T5~HP16CQ0`V3~YIA}()_7L

(2) 连接杆

图2-1 连接板

下图展示了Bricard机构中连接杆的具体设计尺寸。

如图2-2所示，该连接杆为长200mm，直径为5mm的细长圆柱杆，在Bricard机构中起到连接相邻连接板以及整体机构的支撑作用。

图2-2 连接杆

2.1.2 零件材料选择

本组连接板选用亚克力板。亚克力板具有透光性能好、使用寿命长、材料硬度较大等特点。选用亚克力板，能够保证本组设计的连接板在使用寿命内能保持足够的强度。

连接杆选用不锈钢材料。不锈钢材料具有良好的塑性、韧性、焊接性、耐蚀性能弱磁性，并且在氧化性和还原性介质中耐蚀性均较好。选用不锈钢材料，能够保证连接机构具有较好的抗挤压能力和机械性能。

2.1.3 零部件连接方式

本组采用球铰与转动副进行零部件的连接。下图展示了本组设计的球铰剖面（图2-3左）、代球副剖面（图2-3中）与转动副剖面（图2-3右）。

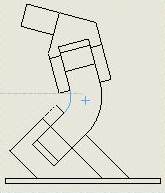
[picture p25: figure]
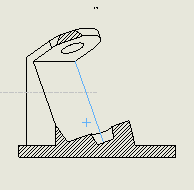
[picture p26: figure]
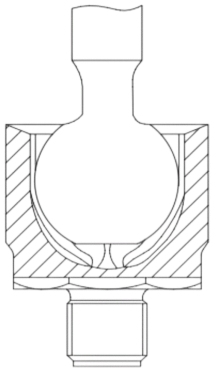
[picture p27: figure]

球铰剖面图 代球副剖面图 转动副剖面图

图2-3 剖面图

2.2 机构整体详细设计

机构初始状态为一截角八面体，其整体构造如图2-4所示。本机构以三重对称 Bricard 连杆机构为折展运动单元，采用 15 个转动副、3个球铰与6个代球副，并以此连接方式实现该可展机构为 1的自由度。

图2-4 带有运动副标记的截角八面体

2.3 关键机构3D模型

2.3.1 零件及其3D模型

（1） 3轴线相交于一点的3转动副代球副（以下简称代球副）

如图2-5所示，该机构上存在3个轴线相交于一点的转动副。在机械功能实现上，该机构能够在球面上进行三个方向的移动。因此，该机构可被利用设计为代球副。

图2-5 代球副3D图

（2） 球铰

如图2-6所示，球铰提供了一个供连接杆插入连接的接口与一个球约束面。该球铰下端与一块带有四个螺孔的底座相接，使得球铰能够被固定在连接面上。

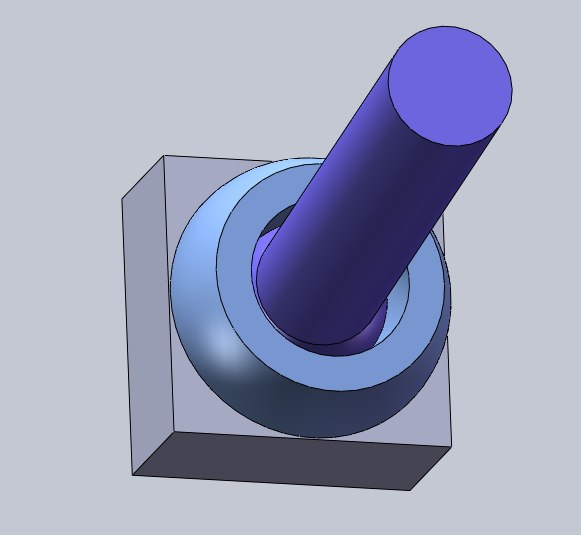
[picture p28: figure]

图2-6 球铰3D图

（3） 转动副

如图2-7所示，转动副提供了一个可沿轴旋转的自由度。该转动副下端同样与带有四个螺孔的底座相接，以起到固定的作用。

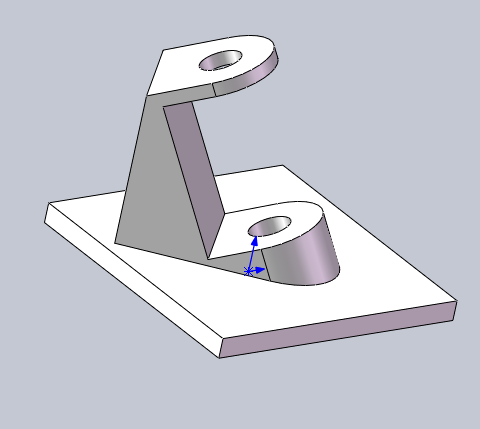
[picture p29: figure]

图2-7 转动副3D图

2.3.2 组合件

如图8所示，该机构是由连接板、连接杆、转动副与球副拼接而成的组合件。该组合件具有2个自由度，能够平移、旋转，并通过连接杆与其他组合件进行拼接，组装成为可展机构基本构件——Bricard机构。图2-8分别展示了该组合件在展开时（左图）与闭合时（右图）的3D模型。

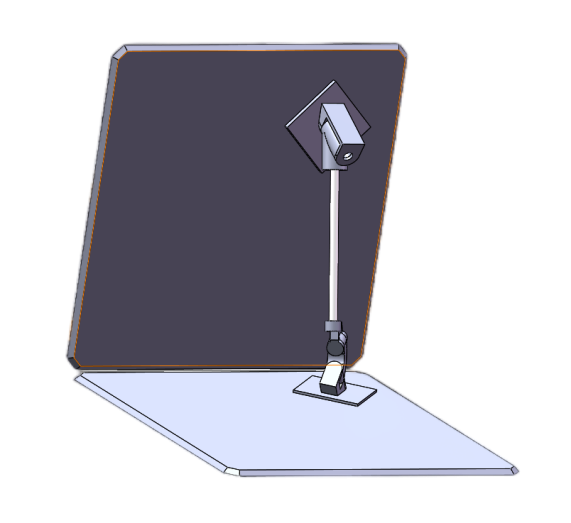
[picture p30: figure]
WPS图片-抠图

图2-8 组合件3D图

2.3.3 单个 Bricard 机构三维模型

如图2-9所示，未展开的Bricard机构由三个组合件拼接而成。Bricard机构包含6个代球副、6个转动副和9根连接杆（暂未标明）。该bricard机构具有2个自由度（可通过转动副替代球副的方式减少其自由度），能够旋转，展开，并通过连接杆与球铰与另一个Bricard机构连接，直接形成可展机构。图9展示了未表明连接杆的单个Bricard机构的3维模型。

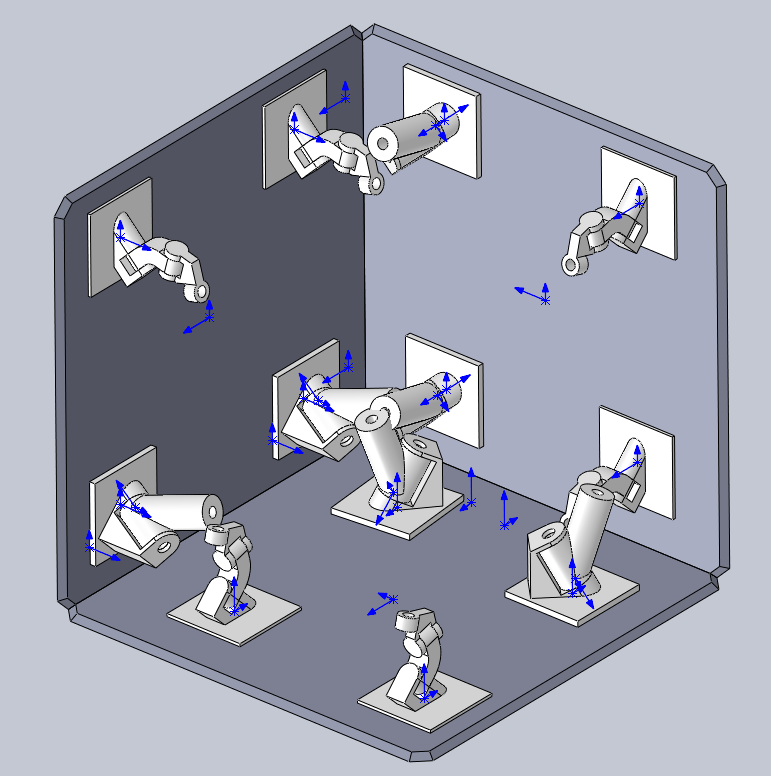
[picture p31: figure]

图2-9 Bricard机构3D图（未展开）

2.4 可展机构3D装配图

WPS图片-抠图

可展机构由2个Bricard机构拼接而成。可展机构未展开时为去掉六角的正方体，展开后则如图2-10所示，呈现出截角八面体的形态。可展机构具有不大于2个的自由度，因而具有较为固定的展开轨迹和展开模型，在实际拼装时可依据本装配图作为是否具有展开形态的标准。

图2-10 可展机构装配图（展开）

2.5 主要零件2D工程图

下图展示了球铰（左上）、代球副（右上）、转动副（左下）以及连接板（右下）的2D平面工程图。如图2-11所示，每张工程图分别从正面、右面以及上方展示了各机构的机械结构与角度、尺寸。此外，每张2D工程图的右下角，通过对各机构斜视图的绘制，展现了该机构的倾斜结构的实形与机械特性。


球铰机构2D工程图

转动副机构2D工程图

连接板机构2D工程图

代球副机构2D工程图

图2-11 各机构2D工程图

2.6 任务情况完成小结

本周期小组完成了可展结构体的三维建模过程，主要包括依据课程报告1中计算得出的转动副大小、坐标位置，确定了零件形状、尺寸、连接方式，并进行了各主要部件对应的2D工程图的绘制。同时，本小组依据已确定的项目规划，安排了下一阶段的任务，暨对可展多面体静力学、动力学以及运动学分析。下面展示了各成员的任务完成情况小结。

刘宇轩：划分任务，完善计算过程和结果；Solidworks设计与建模；负责研讨课展示。

张佳瑜：Solidworks设计、转动副建模；负责模型部分的研讨课展示。

罗松寒：Solidworks设计与建模；负责需求调查产品实现部分的研讨课展；负责课程报告整理。

白韬：负责整理零件、结构设计内容整理和相关部分的研讨课展示。

郭伟祺：Solidworks设计、球副建模；负责模型部分的研讨课展示。

冒惠敏：参与结构设计；负责模型部分课程报告整理。

设计与建造 课程小组会议记录

议题 | | 项目机械设计建模讨论会
组长 | | 刘宇轩 | 年级/班级/组别 | | | 2020级 2 班 第 5 组
组员 | | 郭伟祺 白韬 冒惠敏 罗松寒 张佳瑜
会议时间 | 2022年3月21日 | | | 会议地点 | 郑东图书馆206研究厢
讨论内容 | 本次会议，小组主要对可展多面体的设计建模方法进行讨论，完成了以下工作。 1.讨论了项目任务工作的分配。 2.安排前期调研和第二次课程报告任务。在第一次坐标计算结果的基础上，对项目产品进行了整体结构设计。 3.详细讨论了各部分关键机构设计，如球铰、转动副的形态设计及原理支撑等；对组成机构的零件形状、尺寸、材料、连接方式进行了确定。 4.确定了Bricard机构中进行连接的运动副。 5.进行了在solidworks上的3D模型建立和2D图绘制。
下一步工作计划 | 1.完成可展多面体的静力学、动力学以及运动学分析。 2.准备进行可展多面体展开闭合的运动仿真。
附件材料清单

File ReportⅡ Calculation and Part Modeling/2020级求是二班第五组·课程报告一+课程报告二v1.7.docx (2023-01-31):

设计与建造 课程报告书

天津大学标准校徽

学 院 求是学部

专 业 智能机器平台

年 级 2020级

班级组别 二班5组

小组成员 刘宇轩 罗松寒 郭伟祺

白 韬 冒惠敏 张佳瑜

2020年 3 月 29 日

课程报告1 项目计划

1.1 可展结构资料综述

可展机构在航空航天、建筑、汽车、消防等领域都有着广泛的应用，是人类用以传递力的重要机构。随着全球工业化的快速发展，机械基本上取代了传统的手工的发展，而可展机构为人类生活生产提供了不可忽视的便利性，在航天航空、日常生活, 机器人等领域应用广泛。因此这种机构的机械设计和运动分析研究得到国内研究机构的普遍重视。但对于不同可展机构的开发与应用, 还需要更多针对性的研究与探索。

可展结构的具有众多优秀特性。

（1）结构紧凑、尺寸小巧，且设备收缩后体积小。这是可展机构最大的优点，也使得其作业所要求的占用空间小。在地下水位较高的地区工作时对机坑的处理会十分简单。它能够在任何已有设备上直接使用，而无需修改设备结构和机坑深度。

（2）载荷能力大、稳定性好。相对于其他机构来讲，大部分可展机构的承载能力偏大。由于其稳定的结构，可展机构在额定承载能力和伸展长度下，具有很好的稳定性。

（3）定位精准。大部分可展机构在运行过程能确保在行程的任意一点精确定位，并锁定高度，不像液压设备会因温度的变化或泄漏产生位置变化。

（4）运行平稳、噪音较低。由于其连续成型原理，无垂直方向爬行，使得机构运转平稳安静，除驱动装置的运行噪音，大部分可展器本身的工作噪音很低。

（5）效率高。大部分可展设备的总传动效率较高，通常可达到 80%以上。

（6）构造简单，使用方便。可展机构的结构精巧而简洁，所以可展器本身的安装工作简易而快捷，一块伸缩机构通常在很短的时间即可安装使用。

（7）通用性高。可展机构对使用环境没有太高要求，使其经常在太空、海洋等复杂环境下工作，并依然保持其稳定性。

我们所需要的完成的截角八面体 (由八个六边形和六个四边形围成的十四面体)的体积折展比分别为11.3，可在展开状态下可显著提升工作空间。这些多面体变换过程无运动分叉现象, 具有结构简单和易于控制等特点。通过桁架变换方法，构件可在保持单自由度变换特点的同时降低机构的过约束度数, 从而以较低过约束度甚至非过约束的机构实现变换，减少因过约束带来的制造和装配的苛刻要求，也避免了因构件变形而产生的机构锁死现象，增强了应用的可行性。

1.2 工程师职责

（1）注重产品质量，控制好产品研发进度。

（2）协调各方面工作，确保工作顺利进行。

（3）每周完成组内分配的任务，认真执行计划，按时汇报自己的工作，不因为个人原因拖慢组内进度。

（4）端正工作态度，严谨认真，刻苦钻研，脚踏实地，讲求效率。

（5）正确认识自我，遇到问题及早提出。

1.3 项目管理

项目进度安排甘特图如图1-1 。


图1-1 项目进度安排甘特图

成员分工安排如下：

刘宇轩：组长，负责主管项目进程，组员的任务分配及监督各项任务的完成情况。在具体工作上，负责可展多面体运动简图的描画，三维建模过程，运动学过程分析，力学过程分析，样机设计及制作。

张佳瑜：负责可展多面体运动简图的描画，运动学过程分析，力学过程分析，样机设计及制作。

罗松寒：负责可展多面体运动简图的描画，三维建模过程，运动学过程分析，力学过程分析，样机制作。

白韬：负责可展多面体运动简图的描画，运动学过程分析，力学过程分析，样机制作，可展多面体驱动系统，。

郭伟祺：负责可展多面体运动简图的描画，三维建模过程，运动学过程分析，力学过程分析，样机制作。

冒惠敏：负责可展多面体运动简图的描画，运动学过程分析，力学过程分析，样机设计与制作。

1.4 项目任务书

项目题目——可展机构

1.4.1 用途及功能要求

可展多面体机构在实现其承载功能的前提下，能够大尺寸地改变几何形状与空间构型，以适应不同的应用需求，是空间可折展结构和大型可折展设备的关键技术。单自由度可展多面体机构可以实现单一驱动下两个空间构型的切换，如图一中截角八面体和立方体之间的变换，在展开时可大幅增加工作空间与面积，在完全折叠状态下可减少储存和运输空间。对多面体展开与折叠构型进行分析，确定各顶点的运动副类型及方位，用以形成具有协调运动的多面体空间机构网格。图1-2展示了截角八面体和立方体之间的变换。


图1-2 截角八面体和立方体之间的变换

1.4.2 设计要求和原始数据

（1）设计一种可在截角八面体与立方体之间变换的可展多面体机构；

（2）可展多面体折叠构型下立方体边长200-300mm，机构自由度≤2；

（3）可展多面体折展过程中需避免因零件碰撞而产生的物理干涉；

（4）可展多面体在完全展开状态需保证构型的稳定性。

设计原始数据如下：

表1-1 设计原始数据

方 案 号 | 1－1 | 1－2 | 1－3 | 1－4
整体自由度数 | 1 | 2 | 1 | 2
折叠构型下立方体边长a/mm | 200 | 200 | 300 | 300

1.4.3 设计内容

（1）确定可展多面体折展前后的顶点坐标及多边形单元的基本尺寸；

（2）选定可展多面体顶点处运动副形式，计算转动副空间轴线位置，设计转动副的物理实现形式；

（3）设计合理的零件外形及具体尺寸并确定各类零件数量，避免物理干涉；

（4）设计锁死装置保证可展多面体具有稳定展开构型。

1.4.4 提交的设计结果

（1）可展多面体的机构运动简图，包括顶点处运动副类型，以及转动副空间方位；

（2）可展多面体三维软件建模模型，需包含运动模拟中的3-4个典型折展状态；

（3）可展多面体典型顶点运动轨迹；

（4）可展多面体静力学分析；

（5）各类零件尺寸图若干张；

（6）原理样机；

（7）设计计算说明书，内容包括：

* 设计流程和设计原始数据；

* 可展多面体顶点坐标与各个顶点处转动副的具体轴线方位计算；

* 可展多面体三维建模的过程说明；

* 零件外形及具体尺寸的设计文本。

1.4.5 评价指标及标准

（1）尺寸小、自由度少、体积折展大；

（2）原理样机具有较为规则平整的外观构型；

（3）原理样机能够在最大与最小构型之间折展，且折展过程流畅；

（4）原理样机在完全展开状态应具有较高的稳定性和承载力。

1.5 项目需求分析

表1-2展示了可展多面体的项目需求分析。

表1-2 项目需求分析

需求分析 | 需求表达
机构设计需求 | ① 可展机构 ② 结构体系 ③ 驱动源
用户情况 | 1 面向用户对象 2 使用场合、领域
作品效益 | 1 社会效益及经济效益 2 时间消耗及产出 3 使用频率 4 资金消耗及回报 5 信息使用价值

1.6 产品规格

1.产品体积：可展多面体折叠构型下立方体边长200-300mm，体积大小为8000cm³-27000cm³。

2.产品结构：本机构以三重对称 Bricard 连杆机构为折展运动单元，采用 15 个转动副与 9 个球副。

3.自由度：机构自由度≤2。

4.驱动源:

（1）微电机驱动

在结构上分散或集中布置微电机，直接驱动主动件或通过传动使机构展开或折叠。

（2）弹簧(扭簧、拉簧)元件驱动

在机构节点或杆件中点处按特定要求设詈弹簧元件，折叠时弹簧受预应力存贮弹性变性能；当机构解锁后，弹簧释放弹性能，驱动机构协调同步展开。

（3）自伸展驱动

结构的一部分构件、某些特定构件的中点、整个结构元件，由记忆合金、自适应智能元件等构成，使其在特定环境下可按设计要求自动展开。

5.自锁方式:

（1）有限自锁

在摇杆末端设置一个小凹槽，凹槽位置在转动结束后所在的角度上。在固定 处固定一个细短杆，转动结束后细短杆刚好接到凹槽里。或者在两面之间添加一 个伸缩杆，伸缩杆通过类似装置实现自锁（类比雨伞），从而实现两面高度之间的自锁。

优点：旋转结束后，自锁较稳定。

缺点：回复原六面体有不确定因素。

（2）棘轮自锁

在某一转动副处进行改装，安装一个棘轮。保证转动副只按照特定轨迹单向转动，从而保证在展开的各个阶段都能得到较好的稳定性。此外通过对棘轮的解放，实现由截角八面体到六面体的转换。或者在两个面之间安装连杆装置，通过棘轮实现自锁。

优点：稳定度高，不确定因素少。

缺点：装置复杂，制作过程困难。

（3）涡轮涡杆自锁

在两面之间安装涡轮涡杆结构，通过设计螺旋角和摩擦系数实现自锁。

优点：稳定度高，不确定因素少。

缺点：计算量大，装置复杂。

表1-3展示了项目作品的规格参数表。

表1-3 产品规格参数表

产品规格参数表
产品构件组成 | 零件类型 | 方形面板 | 铰链底座 | 直杆1 | 直杆2 | 直杆3
| 数量(个） | 6 | 24 | 6 | 6 | 3
| 零件类型 | 弯杆1 | 弯杆2 | 螺栓 | 轴承 | 圆柱销
| 数量（个） | 9 | 9 | 96 | 18 | 30
产品数据参数 | 立方体边长 | 自由度 | 驱动源 | 自锁方式 | 折展比 | 折展解构单元
| 280mm | 1 | 微电机 | 棘轮自锁 | 11.314 | 三重对称Bricard连杆机构

1.7 产品概念选择

六步骤选择项目作品概念

步骤一：准备选择矩阵

作品概念评分矩阵表如表1-4

表1-4 概念评分矩阵表

作品概念
选择标准 | 权重 | 自锁方式 | | | | | | 驱动方式
| | 有限自锁 | | 棘轮自锁 | | 涡轮涡杆自锁 | | 微电机驱动 | | 弹簧驱动
| | 评分 | 加权分 | 评分 | 加权分 | 评分 | 加权分 | 评分 | 加权分 | 评分 | 加权分
精确度 | 25% | 3 | 0.075 | 4 | 0.1 | 4 | 0.1 | 4 | 0.1 | 3 | 0.075
稳定性 | 20% | 4 | 0.08 | 5 | 0.1 | 4 | 0.08 | 4 | 0.08 | 3 | 0.06
流畅度 | 15% | 4 | 0.06 | 4 | 0.06 | 5 | 0.075 | 4 | 0.06 | 3 | 0.045
可恢复性 | 10% | 2 | 0.02 | 4 | 0.04 | 4 | 0.04 | 3 | 0.03 | 1 | 0.01
资金预算 | 10% | 5 | 0.05 | 3 | 0.03 | 2 | 0.02 | 2 | 0.02 | 3 | 0.03
计算量 | 10% | 3 | 0.03 | 4 | 0.04 | 2 | 0.02 | 2 | 0.02 | 2 | 0.02
组装难易 | 5% | 4 | 0.02 | 2 | 0.01 | 3 | 0.03 | 2 | 0.01 | 2 | 0.01
整体重量 | 5% | 5 | 0.025 | 4 | 0.02 | 3 | 0.015 | 2 | 0.01 | 4 | 0.02
总评 | 100% | 0.36 | | 0.4 | | 0.38 | | 0.33 | | 0.27
是否采用 | | 否 | | 是 | | 否 | | 是 | | 否

步骤二：作品概念评估

以所有标准，对一个概念评估，然后转向下一个概念。

选择标准：精确度、稳定性、流畅度、可恢复性、资金预算、计算量、组装难易、整体重量。

步骤三：作品概念排序

自锁方式：1.棘轮自锁 2.涡轮涡杆自锁 3.有限自锁

驱动方式：1.微电机驱动 2.弹簧驱动

步骤四：作品概念组合与改进

对作品概念进行组合，保持优势，减少劣势。

步骤五：选出一个作品概念

选择结果：棘轮自锁、微电机驱动

步骤六：反思结果与过程

检查选出的作品概念，确保每位成员满意。

1.8 产品目标指标

1.尺寸：可展多面体折叠构型下立方体边长280mm。

2.自由度：可展机构的自由度为1。

3.驱动源：经过项目作品概念评估矩阵表加权之后权重最高的驱动方式，经评定为微电机驱动的方式。

4.自锁方式：经过项目作品概念评估矩阵表加权之后权重最高的自锁方式，经评定为棘轮自锁的方式。

表1-5展示了项目作品的最终指标。

表1-5 产品最终指标

选择标准 | 指标要求
精确度 | 自锁角度误差小于3%
稳定性 | 展开结构承重极限≥500g
流畅度 | 响应时间≤0.1秒
可恢复性 | 恢复时间≤3秒
产品大小 | 立方体边长≤280mm

1.9 运动副坐标及轴线计算结果

表1-6展示了可展多面体的运动副和运动副轴线的计算结果。详细的计算过程在本报告附件1可展多面体-设计计算说明书中展示。

表1-6 计算结果

运动副空间坐标 | 运动副轴线
A_1^(to) =(√2,(√2)/2,0) | (√2,(√2)/2,0)
A_2^(to) =(√2,0,(√2)/2) | (-3/2,1/2-√2,-1/2-(√2)/2)
A_3^(to) =(√2,-(√2)/2,0) | (√2,-(√2)/2,0)
A_4^(to) =(√2,0,-(√2)/2)
B_1^(to) =(0,√2,(√2)/2) | (0,√2,(√2)/2)
B_2^(to) =((√2)/2,√2,0) | (-1/2-(√2)/2,-3/2,1/2-√2)
B_3^(to) =(0,√2,-(√2)/2) | (0,√2,-(√2)/2)
B_4^(to) =(-(√2)/2,√2,0)
C_1^(to) =((√2)/2,0,√2) | ((√2)/2,0,√2)
C_2^(to) =(0,(√2)/2,√2) | (1/2-√2,-1/2-(√2)/2,-3/2)
C_3^(to) =(-(√2)/2,0,√2) | (-(√2)/2,0,√2)
C_4^(to) =(0,-(√2)/2,√2)
D_1^(to) =(-√2,0,-(√2)/2) | (-√2,0,-(√2)/2)
D_2^(to) =(-√2,-(√2)/2,0) | (3/2,1/2+(√2)/2,-1/2+√2)
D_3^(to) =(-√2,0,(√2)/2)
D_4^(to) =(-√2,(√2)/2,0)
E_1^(to) =(-(√2)/2,-√2,0) | (-(√2)/2,-√2,0)
E_2^(to) =(0,-√2,-(√2)/2) | (-1/2+√2,3/2,1/2+(√2)/2)
E_3^(to) =((√2)/2,-√2,0)
E_4^(to) =(0,-√2,(√2)/2)
F_1^(to) =(0,-(√2)/2,-√2) | (0,-(√2)/2,-√2)
F_2^(to) =(-(√2)/2,0,-√2) | (1/2+(√2)/2,-1/2+√2,3/2)
F_3^(to) =(0,(√2)/2,-√2)
F_4^(to) =((√2)/2,0,-√2)

1.10 设计草图

图1-3、1-4、1-5、1-6、1-7、1-8展示了本组成员绘制的设计草图。

刘宇轩：


图1-3 刘宇轩设计草图

张佳瑜：


图1-4 张佳瑜设计草图

罗松寒：


图1-5 罗松寒设计草图

白韬：


图1-6 白韬设计草图

郭伟祺：


图1-7 郭伟祺设计草图

冒惠敏：


图1-8 冒惠敏设计草图

1.11 任务情况完成小结

本周期小组主要完成了初期项目的准备和管理工作并安排下一阶段的任务，进行各运动副的空间坐标和轴线方向计算并初步确定项目的关键节点确定和时间分配。下面展示了各成员的任务完成情况小结。

刘宇轩：进行组员分工并划分任务，进行会议记录；负责项目综述和项目安排部分的研讨课展示；负责可展多面体的计算工作；负责课程报告一的合稿整理。

张佳瑜：负责需求分析应用领域部分的研讨课展示；负责产品课程报告产品概念内容。

罗松寒：负责需求调查产品实现部分的研讨课展示；负责产品课程报告任务书、项目管理内容。

白韬：负责项目背景部分的研讨课展示；负责产品课程报告产品综述内容。

郭伟祺：负责需求调查产品应用场景与服务对象部分的研讨课展示；负责产品课程报告甘特图、需求表达部分内容。

冒惠敏：负责需求分析产品实现部分的研讨课展示；负责产品课程报告产品规格、目标指标、产品参数部分内容。

设计与建造 课程小组会议记录

议题 | | 项目前期准备讨论会
组长 | | 刘宇轩 | 年级/班级/组别 | | | 2020级 二 班 第 5 组
组员 | | 郭伟祺 白韬 冒惠敏 罗松寒 张佳瑜
会议时间 | 2022年3月9日 18：00-22：30 | | | 会议地点 | 郑东图书馆306研究厢
讨论内容 | 会议围绕初期的项目准备以及任务分配问题展开，主要讨论并解决了以下内容。 1.讨论了项目任务工作的分配。 2.安排前期调研和第一次课程报告任务，以及计算可展多面体顶点和运动副的空间坐标。 3.确定项目管理与时间规划，评估并分配各个项目的时间并制作甘特图。
下一步工作计划 | 1.完成可展多面体的设计计算 2.使用solidworks对项目多面体进行建模。
附件材料清单 | 附件1：可展多面体-设计计算说明书

参考文献

[1]朱严宽,刘树青,陈伟,薛海峰.可展机构研究综述[J].科技创新与应用,2017(17):62-63.

附件1：可展多面体-设计计算说明书

理论计算部分

1 体积折展比

设计方案选择截角八面体和立方体之间的变换，设正多边形边长为a, 截角八面体体积为 8√2a^3 ，立方体体积为 a^3 ，则理论体积折展比为 8√2≈11.314 。

2 两种构型下各顶点坐标

如图1.9所示，在截角八面体中，每个六边形面（如 A_1 A_2 C_1 C_2 B_1 B_2 ）被三个正方形面和三个连接杆包围，呈现出三重对称性。如果把这些六边形的白色面折叠起来，剩下的六个正方形蓝色面就会形成一个立方体。因此，我们将从三重对称Bircard机构开始构造具有多环连杆的多面体变换方案。


图1-9 截角八面体和立方体之间的变换

一个截角八面体和一个具有单位长度边的立方体，如果在变换期间没有发生干涉，则其顶点运动前后的坐标是唯一的，并且所有的八个六边形空洞将在转变后消失。使用图1-9中所示的笛卡尔坐标系，通过顶点的位置可以更好地说明多面体之间的转换。

当多面体的每边都有单位长度时，截角八面体所有24个顶点坐标为：（其中上角标“to”表示截角八面体—truncated octahedron。）

A_1^(to) =(√2,(√2)/2,0)

A_2^(to) =(√2,0,(√2)/2)

A_3^(to) =(√2,-(√2)/2,0)

A_4^(to) =(√2,0,-(√2)/2)

B_1^(to) =(0,√2,(√2)/2)

B_2^(to) =((√2)/2,√2,0)

B_3^(to) =(0,√2,(√2)/2)

B_4^(to) =(-(√2)/2,√2,0)

C_1^(to) =((√2)/2,0,√2)

C_2^(to) =(0,(√2)/2,√2)

C_3^(to) =(-(√2)/2,0,√2)

C_4^(to) =(0,-(√2)/2,√2)

D_1^(to) =(-√2,0,-(√2)/2)

D_2^(to) =(-√2,-(√2)/2,0)

D_3^(to) =(-√2,0,(√2)/2)

D_4^(to) =(-√2,(√2)/2,0)

E_1^(to) =(-(√2)/2,-√2,0)

E_2^(to) =(0,-√2,-(√2)/2)

E_3^(to) =((√2)/2,-√2,0)

E_4^(to) =(0,-√2,(√2)/2)

F_1^(to) =(0,-(√2)/2,-√2)

F_2^(to) =(-(√2)/2,0,-√2)

F_3^(to) =(0,(√2)/2,-√2)

F_4^(to) =((√2)/2,0,-√2)

3 Bricard机构的配置

首先，让我们从六边形面 A_1 A_2 C_1 C_2 B_1 B_2 开始配置Bricard机构。如图1-10所示，它的初始形状是一个正六边形，变换后，顶点 A_1 , C_1 , B_1 收敛到立方体上的一个顶点（如图1.9右图所示）。因此，该六边形面的运动将具有三重对称性。在这些顶点配置转动关节后，为了实现预期运动，所形成的折展运动单元必须是三重对称Bricard连杆机构。


图1-10 六边形面 A_1 A_2 C_1 C_2 B_1 B_2 处的Bricard机构

图1-11显示了截角八面体的正方形B和C，以及在坐标系中固定B1C2时它们的最终位置。当正方形B围绕 B1关节轴线旋转时，顶点 B4 转到 C2，可得到 B_4^(') =C_2^(to) =TB_4^(to) 和 B_1^(') =TB_1^(to) ，则3×3变换矩阵T为：


图1-11 正方形B和C绕 B1 ,C2绕旋转后的最终位置

T=[-2/3, -1/3, 2/31/3, 2/3, 2/3-2/3, 2/3, -1/3]

利用T进而求得 B_2^(') 的位置为

B_2^(') =TB_2^(to) = (-2/3√2,5/6√2,1/3√2)

最终位置的正方形B和C形成立方体的两个垂直面，于是有

B_1^(to) C_4^(') =B_1^(to) C_2^(to) ×B_1^(to) B_2^(') _2

则 C_4^(') 的最终位置为

C_4^(') =(1/3,-2/3+√2,(√2)/2-2/3)

正方形C沿着 C2处转动关节做整体刚性转动，所以轴线位置 s_(C2) 为 C_1^(to) C_1^(') 和 C_4^(to) C_4^(') 公垂线方向，则可得到

s_(C2) =(1/2-√2,-1/2-(√2)/2,-3/2)

由于Bricard机构的三重对称性，如图1-9中坐标系所示，假设六边形面 A_1 A_2 C_1 C_2 B_1 B_2 处的机构绕向量 (1, 1, 1)^T （六边形面法线方向）整体旋转120°，则 s_(B1) 转到 s_(C1) ， s_(C1) 转到 s_(A1) ，那么有 s_(C1) =T_1 s_(B1) 和 s_(A1) =T_1 s_(C1) ，此变换矩阵T1为

T_1 =[0, 0, 11, 0, 00, 1, 0]

利用同样的120°旋转变换， s_(C2) 则转到 s_(A2) ， s_(A2) 转到 s_(B2) ，就可得到A2 和B2处转动副轴线方向

s_(A2) =T_1 s_(C2) =(-3/2,1/2-√2,-1/2-(√2)/2)

s_(B2) =T_1 s_(A2) =(-1/2-(√2)/2,-3/2,1/2-√2)

由于图1-9中六边形D1D2E1E2F1F2与A1A2C1C2B1B2不直接连接，且这两个六边形的结构是相同的，因此在六角边形D1D2E1E2F1F2设置相同的Bricard机构。利用三维对称性，2个六边形处的Bricard机构关于坐标原点对称，其中 s_(D1) ,s_(E1) ,s_(F1) 依然相交于坐标原点并分别指向各自对应顶点，则其各个顶点处转动关节的轴线可按照上述求解过程同理可得：

s_(D1) =(-√2,0,-(√2)/2)

s_(D2) =(3/2,1/2+(√2)/2,-1/2+√2)

s_(E1) =(-(√2)/2,-√2,0)

4 整体系统的机构网格

到目前为止，为构造多面体连杆机构，已经求得两个相同的三重对称Bricard机构的转动轴线位置，如图1-12所示，除Bricard机构所含的转动关节（12个），其余顶点则暂时设置为球副。计算机模拟后，此可折展多面体具有两个自由度。进一步的，利用对称性，将A3 , B3 和C3处的球副替换转动副，可得到单自由度系统。


图1-12 包含两个Bricard机构的整体多面体构造

其中，与B1的轴线方位相似，A3处转动关节可平分∠A2A3E3并指向多面体中心，则杆A2A3与杆E3A3绕其转动后可重合。同理，A3，B3，C3处转动关节相交于坐标原点并分别指向各自对应顶点，则有

s_(A3) =(√2,-(√2)/2,0)

s_(B3) =(0,√2,-(√2)/2)

s_(C3) =(-(√2)/2,0,√2)

课程报告2 三维建模

2.1 产品零件的确定与连接方式选择

2.1.1 零件形状及尺寸

(1)连接板

下图展示了Bricard机构中关键连接板的具体设计尺寸。

如图2-1所示，该连接板长、宽均为200mm，厚3mm的正方形板，并在四角处切掉了长为5mm的等腰直角三角形，以防止在展开时可能存在的的机构干涉现象发生。

T5~HP16CQ0`V3~YIA}()_7L

(2) 连接杆

图2-1 连接板

下图展示了Bricard机构中连接杆的具体设计尺寸。

如图2-2所示，该连接杆为长200mm，直径为5mm的细长圆柱杆，在Bricard机构中起到连接相邻连接板以及整体机构的支撑作用。

WPS图片-抠图

图2-2 连接杆

2.1.2 零件材料选择

本组连接板选用亚克力板。亚克力板具有透光性能好、使用寿命长、材料硬度较大等特点。选用亚克力板，能够保证本组设计的连接板在使用寿命内能保持足够的强度。

连接杆选用不锈钢材料。不锈钢材料具有良好的塑性、韧性、焊接性、耐蚀性能弱磁性，并且在氧化性和还原性介质中耐蚀性均较好。选用不锈钢材料，能够保证连接机构具有较好的抗挤压能力和机械性能。

2.1.3 零部件连接方式

本组采用球铰与转动副进行零部件的连接。下图展示了本组设计的球铰剖面（图2-3左）、代球副剖面（图2-3中）与转动副剖面（图2-3右）。


球铰剖面图 代球副剖面图 转动副剖面图

图2-3 剖面图

2.2 机构整体详细设计

机构初始状态为一截角八面体，其整体构造如图2-4所示。本机构以三重对称 Bricard 连杆机构为折展运动单元，采用 15 个转动副、3个球铰与6个代球副，并以此连接方式制作自由度为1的可展机构。

图2-4 带有运动副标记的截角八面体

2.3 关键机构3D模型

2.3.1 零件及其3D模型

（1） 3轴线相交于一点的3转动副代球副（以下简称代球副）

如图2-5所示，该机构上存在3个轴线相交于一点的转动副。在机械功能实现上，该机构能够在球面上进行三个方向的移动。因此，该机构可被利用设计为代球副。


图2-5 代球副3D图

（2） 球铰

如图2-6所示，球铰提供了一个供连接杆插入连接的接口与一个球约束面。该球铰下端与一块带有四个螺孔的底座相接，使得球铰能够被固定在连接面上。

图2-6 球铰3D图

（3） 转动副

如图2-7所示，转动副提供了一个可沿轴旋转的自由度。该转动副下端同样与带有四个螺孔的底座相接，以起到固定的作用。


图2-7 转动副3D图

2.3.2 组合件

如图8所示，该机构是由连接板、连接杆、转动副与球副拼接而成的组合件。该组合件具有2个自由度，能够平移、旋转，并通过连接杆与其他组合件进行拼接，组装成为可展机构基本构件——Bricard机构。图2-8分别展示了该组合件在展开时（左图）与闭合时（右图）的3D模型。

WPS图片-抠图

图2-8 组合件3D图

2.3.3 单个 Bricard 机构三维模型

如图2-9所示，未展开的Bricard机构由三个组合件拼接而成。Bricard机构包含6个代球副、6个转动副和9根连接杆（暂未标明）。该Bricard机构具有2个自由度（可通过转动副替代球副的方式减少其自由度），能够旋转、展开，并通过连接杆与球铰与另一个Bricard机构连接，直接形成可展机构。图9展示了未表明连接杆的单个Bricard机构的3维模型。


图2-9 Bricard机构3D图（未展开）

2.4 可展机构3D装配图

可展机构由2个Bricard机构拼接而成。可展机构未展开时为去掉六角的正方体，展开后则如图2-10所示，呈现出截角八面体的形态。可展机构具有不大于2个的自由度，因而具有较为固定的展开轨迹和展开模型。在实际拼装时可依据本装配图作为是否具有正确展开形态的标准。

图2-10 可展机构装配图（展开）

2.5 主要零件2D工程图

下图展示了球铰（左上）、代球副（右上）、转动副（左下）以及连接板（右下）的2D平面工程图。如图2-11所示，每张工程图分别从正面、右面以及上方展示了各机构的机械结构与角度、尺寸。此外，每张2D工程图的右下角，通过对各机构斜视图的绘制，展现了该机构的倾斜结构的实形与机械特性。


球铰机构2D工程图

转动副机构2D工程图

连接板机构2D工程图

代球副机构2D工程图

图2-11 各机构2D工程图

2.6 任务情况完成小结

本周期小组完成了可展结构体的三维建模过程，主要包括依据课程报告1中计算得出的转动副大小、坐标位置，确定了零件形状、尺寸、连接方式，并进行了各主要部件对应的2D工程图的绘制。同时，本小组依据已确定的项目规划，安排了下一阶段的任务，暨对可展多面体静力学、动力学以及运动学分析。下面展示了各成员的任务完成情况小结。

刘宇轩：划分任务，完善计算过程和结果；Solidworks设计与建模；负责研讨课展示。

张佳瑜：Solidworks设计、转动副建模；负责模型部分的研讨课展示。

罗松寒：Solidworks设计与建模；负责需求调查产品实现部分的研讨课展示；负责课程报告整理。

白韬：负责整理零件、结构设计内容整理和相关部分的研讨课展示。

郭伟祺：Solidworks设计、球副建模；负责模型部分的研讨课展示。

冒惠敏：参与结构设计；负责模型部分课程报告整理。

设计与建造 课程小组会议记录

议题 | | 项目机械设计建模讨论会
组长 | | 刘宇轩 | 年级/班级/组别 | | | 2020级 二 班 第 5 组
组员 | | 郭伟祺 白韬 冒惠敏 罗松寒 张佳瑜
会议时间 | 2022年3月21日 18：00-22：30 | | | 会议地点 | 郑东图书馆206研究厢
讨论内容 | 本次会议，小组主要对可展多面体的设计建模方法进行讨论，完成了以下工作。 1.讨论了项目任务工作的分配。 2.安排前期调研和第二次课程报告任务。在第一次坐标计算结果的基础上，对项目产品进行了整体结构设计。 3.详细讨论了各部分关键机构设计，如球铰、转动副的形态设计及原理支撑等；对组成机构的零件形状、尺寸、材料、连接方式进行了确定。 4.确定了Bricard机构中进行连接的运动副。 5.进行了在solidworks上的3D模型建立和2D图绘制。
下一步工作计划 | 1.完成可展多面体的静力学、动力学以及运动学分析。 2.准备进行可展多面体展开闭合的运动仿真。
附件材料清单 | 无

参考文献

[1]孙学敏,李锐明,姚燕安.面对称Bricard-like机构的设计与研究[J].机械工程学报,2021,57(21):78-87.

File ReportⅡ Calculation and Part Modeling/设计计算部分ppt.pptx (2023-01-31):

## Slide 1

设计与建造Ⅱ·可展机构
课程报告二

设计与建造二班五组
刘宇轩 张佳瑜 罗松寒
冒惠敏 郭伟祺 白 韬

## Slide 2

可展结构——设计计算

（1）体积折展比 设计方案选择截角八面体和立方体之间的变换，设正多边形边长为a, 截角八面体体积为 8√2a^3 ，立方体体积为 a^3 ，则理论体积折展比为 8√2≈11.314 。

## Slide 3

可展结构——设计计算

（2）运动副空间坐标

A_1^(to) =(√2,(√2)/2,0) A_2^(to) =(√2,0,(√2)/2) A_3^(to) =(√2,−(√2)/2,0) A_4^(to) =(√2,0,−(√2)/2) B_1^(to) =(0,√2,(√2)/2) B_2^(to) =((√2)/2,√2,0) B_3^(to) =(0,√2,(√2)/2) B_4^(to) =(−(√2)/2,√2,0)

C_1^(to) =((√2)/2,0,√2) C_2^(to) =(0,(√2)/2,√2) C_3^(to) =(−(√2)/2,0,√2) C_4^(to) =(0,−(√2)/2,√2) D_1^(to) =(−√2,0,−(√2)/2) D_2^(to) =(−√2,−(√2)/2,0) D_3^(to) =(−√2,0,(√2)/2) D_4^(to) =(−√2,(√2)/2,0)

E_1^(to) =(−(√2)/2,−√2,0) E_2^(to) =(0,−√2,−(√2)/2) E_3^(to) =((√2)/2,−√2,0) E_4^(to) =(0,−√2,(√2)/2) F_1^(to) =(0,−(√2)/2,−√2) F_2^(to) =(−(√2)/2,0,−√2) F_3^(to) =(0,(√2)/2,−√2) F_4^(to) =((√2)/2,0,−√2)

当多面体的每边都有单位长度时，截角八面体所有24个顶点坐标如左式所示。（其中上角标“to”表示截角八面体—truncated octahedron）

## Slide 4

可展结构——设计计算

（3）Bricard机构配置

为了实现预期运动，所形成的折展运动单元必须是三重对称Bricard连杆机构。
右图显示了截角八面体的正方形B和C，以及在坐标系中固定B1C2时它们的最终位置。当正方形B围绕 B1关节轴线旋转时，顶点 B4 转到 C2，可得到 B_4^(′) =C_2^(to) =TB_4^(to) 和 B_1^(′) =TB_1^(to) ，则3×3变换矩阵T和 B_2^(′) 位置为：

T=[−2/3, −1/3, 2/31/3, 2/3, 2/3−2/3, 2/3, −1/3]

B_2^(′) =TB_2^(to) = (−2/3√2,5/6√2,1/3√2)


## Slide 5

可展结构——设计计算

（3）Bricard机构配置

正方形B和C形成立方体的两个垂直面，有

则 C_4^(′) 的最终位置为

C_4^(′) =(1/3,−2/3+√2,(√2)/2−2/3)

正方形C沿着 C2处转动关节做整体刚性转动，所以轴线位置 s_(C2) 为 C_1^(to) C_1^(′) 和 C_4^(to) C_4^(′) 公垂线方向，则可得到

利用同样的120°旋转变换， s_(C2) 则转到 s_(A2) ， s_(A2) 转到 s_(B2) ，就可得到其他处转动副轴线方向

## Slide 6

可展结构——设计计算

（4）双自由度消除为单自由度

利用对称性，将A3 , B3 和C3处的球副替换转动副，可得到单自由度系统。


DoF=1
减少3球副

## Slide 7

可展结构——设计计算

（5）结果

运动副空间坐标 | 运动副轴线
A_1^(to) =(√2,(√2)/2,0) | (√2,(√2)/2,0)
A_2^(to) =(√2,0,(√2)/2) | (−3/2,1/2−√2,−1/2−(√2)/2)
A_3^(to) =(√2,−(√2)/2,0) | (√2,−(√2)/2,0)
A_4^(to) =(√2,0,−(√2)/2)
B_1^(to) =(0,√2,(√2)/2) | (0,√2,(√2)/2)
B_2^(to) =((√2)/2,√2,0) | (−1/2−(√2)/2,−3/2,1/2−√2)
B_3^(to) =(0,√2,−(√2)/2) | (0,√2,−(√2)/2)
B_4^(to) =(−(√2)/2,√2,0)
C_1^(to) =((√2)/2,0,√2) | ((√2)/2,0,√2)
C_2^(to) =(0,(√2)/2,√2) | (1/2−√2,−1/2−(√2)/2,−3/2)
C_3^(to) =(−(√2)/2,0,√2) | (−(√2)/2,0,√2)
C_4^(to) =(0,−(√2)/2,√2)

运动副空间坐标 | 运动副轴线
D_1^(to) =(−√2,0,−(√2)/2) | (−√2,0,−(√2)/2)
D_2^(to) =(−√2,−(√2)/2,0) | (3/2,1/2+(√2)/2,−1/2+√2)
D_3^(to) =(−√2,0,(√2)/2)
D_4^(to) =(−√2,(√2)/2,0)
E_1^(to) =(−(√2)/2,−√2,0) | (−(√2)/2,−√2,0)
E_2^(to) =(0,−√2,−(√2)/2) | (−1/2+√2,3/2,1/2+(√2)/2)
E_3^(to) =((√2)/2,−√2,0)
E_4^(to) =(0,−√2,(√2)/2)
F_1^(to) =(0,−(√2)/2,−√2) | (0,−(√2)/2,−√2)
F_2^(to) =(−(√2)/2,0,−√2) | (1/2+(√2)/2,−1/2+√2,3/2)
F_3^(to) =(0,(√2)/2,−√2)
F_4^(to) =((√2)/2,0,−√2)

右表展示了最终的计算结果。

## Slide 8

可展结构——任务分配与合作

本周期小组主要完善了可展多面体的计算，考虑零部件和标准件的材料、连接方式选择并开始可展多面体的3D建模，下面展示了各成员的任务完成情况小结。
刘宇轩：划分任务，完善计算过程和结果；Solidworks设计与建模；负责研讨课展示。
张佳瑜：Solidworks设计、转动副建模；负责模型部分的研讨课展示。
罗松寒： Solidworks设计与建模；负责需求调查产品实现部分的研讨课展；负责课程报告整理。
白韬：负责整理零件、结构设计内容整理和相关部分的研讨课展示。
郭伟祺：Solidworks设计、球副建模；负责模型部分的研讨课展示。
冒惠敏：参与结构设计；负责模型部分课程报告整理。


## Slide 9

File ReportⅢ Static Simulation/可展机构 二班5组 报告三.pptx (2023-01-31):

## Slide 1

设计与建造Ⅱ·可展机构
课程报告三 仿真

设计与建造二班五组
刘宇轩 张佳瑜 罗松寒
冒惠敏 郭伟祺 白 韬

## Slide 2

可展结构——仿真工作思路

（1）sw绘制一个截角八面体。
（2）把单位长度的板和连接杆贴合到截角八面体上，去除截角八面体。
（3）球副位置设置 点重合 约束，转动副位置设置三个角度约束。
（4）力学分析：应力、应变和位移分析。
（5）动力学分析：计算角度，一个转动副利用三个角度配合代替。


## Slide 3

可展结构——截角八面体


配合
+
解除配合


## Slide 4

设计零件的静力学分析


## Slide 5

设计零件的静力学分析


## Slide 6

设计零件的静力学分析


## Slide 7

可展结构——运动副


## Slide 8

可展结构——运动副


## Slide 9

可展结构——运动副


1类转动副（以C1为例）
α=β=γ=angle(((√2)/2,0,√2),(−1,1,0))
2类转动副（以C2为例）
α=β=angle ((1/2−√2,−1/2−(√2)/2,−3/2),(0,1,−1))
γ=angle((1/2−√2,−1/2−(√2)/2,−3/2),(−1,−1,0))

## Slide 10

可展结构——运动副

1类转动副
α=β=γ=71.56505118°
2类转动副
α=β=84.42382381°
γ=45.27049248°

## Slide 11

可展结构——运动副


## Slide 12

可展结构——运动副


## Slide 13

可展结构——运动副


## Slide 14

可展结构——运动副


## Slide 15

可展结构——任务分配与合作

本周期小组主要修改了工作逻辑，对十四面体外壳建模，进行静力学分析，添加转动副，尝试运动学分析仿真。
刘宇轩：划分任务，截角八面体设计和建模，转动副调试，PPT制作和会议记录。
张佳瑜：截角八面体建模、转动副设计和建模。
罗松寒：应力、应变、位移仿真。
白韬：PPT制作，整理工作逻辑。
郭伟祺：运动学仿真建模，转动副调试。
冒惠敏：转动副设计和建模，转动副调试。


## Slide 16

Thanks

敬请批评指正

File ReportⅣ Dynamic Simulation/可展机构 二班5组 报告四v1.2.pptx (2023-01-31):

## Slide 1

电路与电子Ⅲ·肌电
项目答辩

电路与电子
刘宇轩 张佳瑜 罗松寒
冒惠敏 郭伟祺 白 韬

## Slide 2

项目背景

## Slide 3

项目背景

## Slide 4

项目背景

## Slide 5

项目规划

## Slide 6

项目实施过程

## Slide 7

产品测试一：抽奖装置

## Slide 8

产品测试一：抽奖装置

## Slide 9

产品测试二：护理监护装置

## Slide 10

产品测试二：护理监护装置

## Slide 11

Thanks

敬请批评指正

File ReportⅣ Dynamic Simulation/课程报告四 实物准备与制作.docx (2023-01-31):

课程报告四 实物准备与制作

4.1 零件材料与规格

4.1.1 部分关键零件材料规格表

本组使用的3D打印所需的聚乳酸材料的性能指标如表4-1所示。

表4-1 聚乳酸材料性能

属性 | 数值 | 单位
弹性模量 | 3160000000 | N/(m^2)
中泊松比 | 0.32 | 无
中抗剪模量 | 1190 | N/(m^2)
张力强度 | 75000000 | N/(m^2)
屈服强度 | 54～170 | MPa
热膨胀系数 | 0.002256 | W/((mk))

用于连接运动副的铝合金杆的材料性能如表4-2所示。

表4-2 铝合金材料性能

属性 | 数值 | 单位
弹性模量 | 10000000 | N/(m^2)
中泊松比 | 0.3897 | 无
中抗剪模量 | 27000000000 | N/(m^2)
张力强度 | 75000000 | N/(m^2)
屈服强度 | 2500000000000 | N/(m^2)
热膨胀系数 | 0.000045 | W/((mk))

4.1.2零件规格表

实物制作中使用的所有零件规格表如表4-3所示。

表4-3 零件清单

零件 | 尺寸/mm | 数量
3D打印材料 | | 约0.5kg
Ⅰ类转动副的连接轴 | 标准件 | 6个
Ⅱ类转动副的连接轴 | 标准件 | 6个
球副的连接轴 | 标准件 | 24个
亚克力板 | 230*230*4 | 6个
铝合金杆 | D=5, h=180 | 12个
螺栓 | M3*10 | 4*4*6=96个
剪式升降机构 | 标准件 | 1个
转盘轴承 | D=600 | 1个

4.2关键零件与装配

4.2.1关键零件

4.2.1.1转动副

4.2.1.2升降机构

4.2.2零件配合

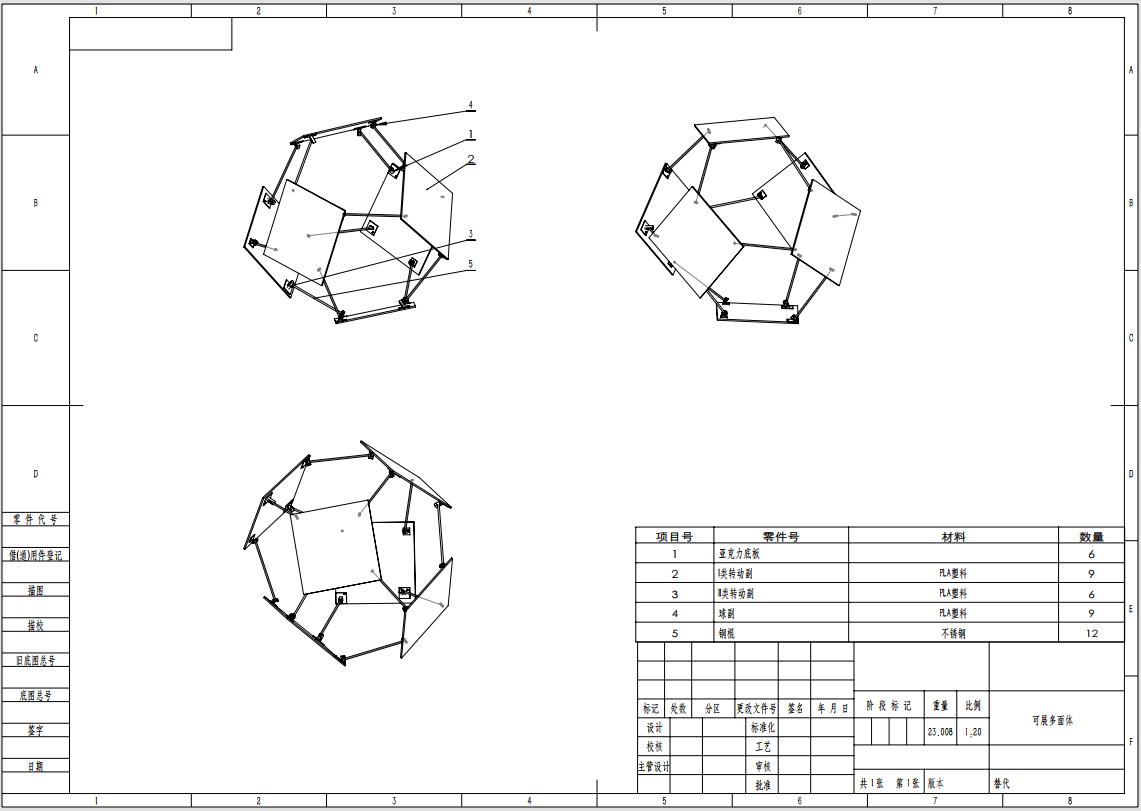
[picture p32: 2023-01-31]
pic and video/Engineering Drawings.png

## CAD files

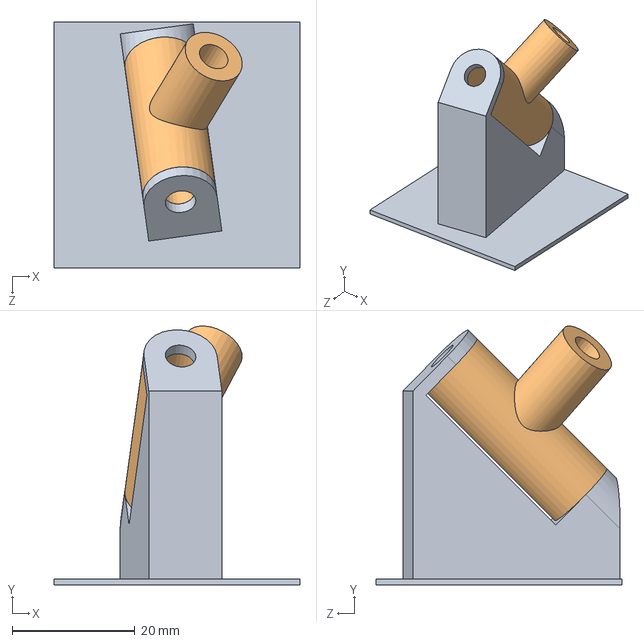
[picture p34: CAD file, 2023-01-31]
ReportⅣ Dynamic Simulation/转动副A/转动副A.SLDASM
40.0 x 42.1 x 40.0 mm
转动副A1
转动副A2

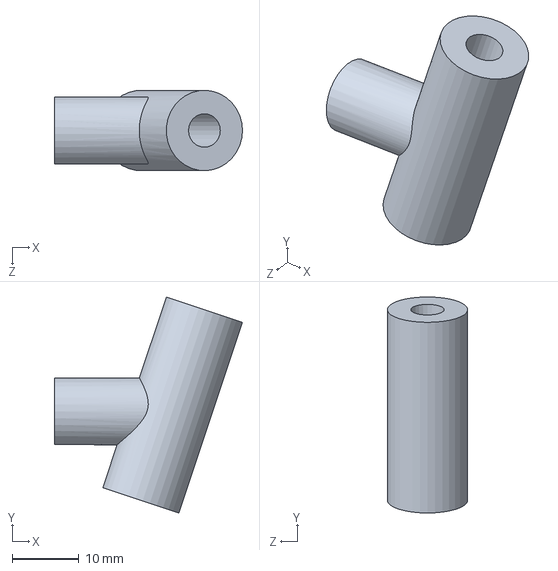
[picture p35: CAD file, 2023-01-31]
ReportⅣ Dynamic Simulation/转动副A/转动副A3.SLDPRT
28.1 x 32.2 x 12.0 mm

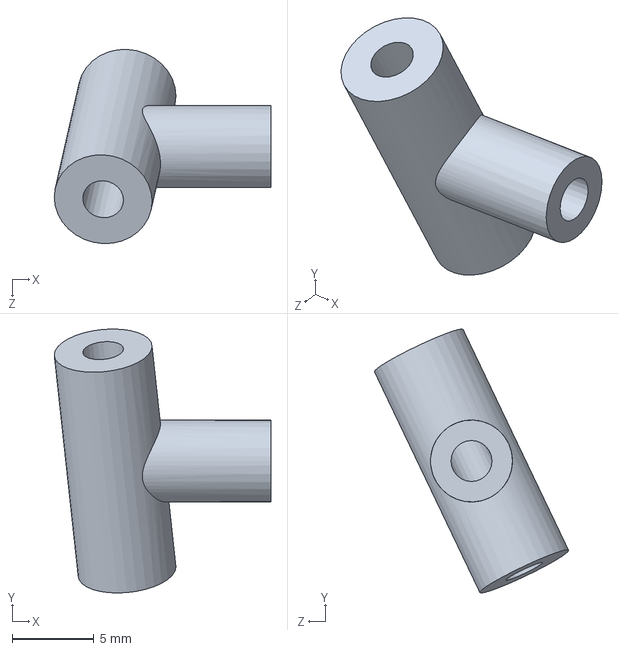
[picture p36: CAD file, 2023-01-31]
ReportⅣ Dynamic Simulation/转动副A/转动副A2.SLDPRT
13.2 x 16.1 x 11.8 mm

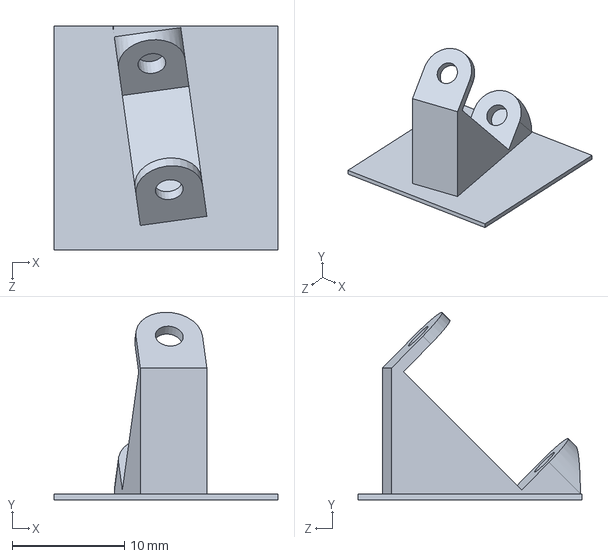
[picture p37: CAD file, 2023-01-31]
ReportⅣ Dynamic Simulation/转动副A/转动副A1.SLDPRT
20.0 x 16.7 x 20.0 mm

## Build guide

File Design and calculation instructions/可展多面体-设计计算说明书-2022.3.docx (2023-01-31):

一、项目作品详细设计

计算过程与说明 | 结果


理论计算部分 1 体积折展比 设计方案选择截角八面体和立方体之间的变换，设正多边形边长为a, 截角八面体体积为 8√2a^3 ，立方体体积为 a^3 ，则理论体积折展比为 8√2≈11.314 。 2 两种构型下各顶点坐标 如图1.1所示，在截角八面体中，每个六边形面（如 A_1 A_2 C_1 C_2 B_1 B_2 ）被三个正方形面和三个连接杆包围，呈现出三重对称性。如果把这些六边形的白色面折叠起来，剩下的六个正方形蓝色面就会形成一个立方体。因此，我们将从三重对称Bircard机构开始构造具有多环连杆的多面体变换方案。 图1.1 截角八面体和立方体之间的变换 一个截角八面体和一个具有单位长度边的立方体，如果在变换期间没有发生干涉，则其顶点运动前后的坐标是唯一的，并且所有的八个六边形空洞将在转变后消失。使用图1.1中所示的笛卡尔坐标系，通过顶点的位置可以更好地说明多面体之间的转换。

计算过程与说明 | 结果
当多面体的每边都有单位长度时，截角八面体所有24个顶点坐标为：（其中上角标“to”表示截角八面体—truncated octahedron。） A_1^(to) =(√2,(√2)/2,0) A_2^(to) =(√2,0,(√2)/2) A_3^(to) =(√2,-(√2)/2,0) A_4^(to) =(√2,0,-(√2)/2) B_1^(to) =(0,√2,(√2)/2) B_2^(to) =((√2)/2,√2,0) B_3^(to) =(0,√2,(√2)/2) B_4^(to) =(-(√2)/2,√2,0) C_1^(to) =((√2)/2,0,√2) C_2^(to) =(0,(√2)/2,√2) C_3^(to) =(-(√2)/2,0,√2) C_4^(to) =(0,-(√2)/2,√2) D_1^(to) =(-√2,0,-(√2)/2) D_2^(to) =(-√2,-(√2)/2,0) D_3^(to) =(-√2,0,(√2)/2) D_4^(to) =(-√2,(√2)/2,0) E_1^(to) =(-(√2)/2,-√2,0) E_2^(to) =(0,-√2,-(√2)/2) E_3^(to) =((√2)/2,-√2,0) E_4^(to) =(0,-√2,(√2)/2) F_1^(to) =(0,-(√2)/2,-√2) F_2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

计算过程与说明 | 结果


图1.2 六边形面 A_1 A_2 C_1 C_2 B_1 B_2 处的Bricard机构 接下来，通过确定每个转动关节的方向以满足Bricard机构运动条件。以顶点 B1为例说明，转换为立方体后，边B1C2和B1B4必须共线，这就要求B1处的转动关节轴线在其平分角上。同时，由于该机构的三重对称性，轴线必须位于包含B1, O 和 A2的平面上。因此， A_1 , B_1 , C_1 处转动副的方向相交于坐标原点并分别指向各个顶点，则转动副轴线 s_(A1) ,s_(B1) ,s_(C1) 可表示为： s_(A1) =(√2,(√2)/2,0) s_(B1) =(0,√2,(√2)/2) s_(C1) =((√2)/2,0,√2) 图1.3显示了截角八面体的正方形B和C，以及在坐标系中固定B1C2时它们的最终位置。当正方形B围绕 B1关节轴线旋转时，顶点 B4 转到 C2，可得到 B_4^(') =C_2^(to) =TB_4^(to) 和 B_1^(') =TB_1^(to) ，则3×3变换矩阵T为：

计算过程与说明 | 结果


图1.3 正方形B和C绕 B1 ,C2绕旋转后的最终位置 T=[-2/3, -1/3, 2/31/3, 2/3, 2/3-2/3, 2/3, -1/3] 利用T进而求得 B_2^(') 的位置为 B_2^(') =TB_2^(to) = (-2/3√2,5/6√2,1/3√2) 最终位置的正方形B和C形成立方体的两个垂直面，此时 C_1^(') C_4^(') ⊥C_1^(') C_2^(') 和 C_1^(') C_4^(') ⊥B_1^(') B^(') _2 ，因为 B_1^(to) =B^(') _1 =C_1^(') ，于是有 B_1^(to) C_4^(') =B_1^(to) C_2^(to) ×B_1^(to) B_2^(') _2 则 C_4^(') 的最终位置为 C_4^(') =(1/3,-2/3+√2,(√2)/2-2/3)

计算过程与说明 | 结果

正方形C沿着 C2处转动关节做整体刚性转动，所以轴线位置 s_(C2) 为 C_1^(to) C_1^(') 和 C_4^(to) C_4^(') 公垂线方向，则可得到

s_(C2) =(1/2-√2,-1/2-(√2)/2,-3/2)

由于Bricard机构的三重对称性，如图1.2中坐标系所示，假设六边形面 A_1 A_2 C_1 C_2 B_1 B_2 处的机构绕向量 (1, 1, 1)^T （六边形面法线方向）整体旋转120°，则 s_(B1) 转到 s_(C1) ， s_(C1) 转到 s_(A1) ，那么有 s_(C1) =T_1 s_(B1) 和 s_(A1) =T_1 s_(C1) ，此变换矩阵T1为

T_1 =[0, 0, 11, 0, 00, 1, 0]

利用同样的120°旋转变换， s_(C2) 则转到 s_(A2) ， s_(A2) 转到 s_(B2) ，就可得到A2 和B2处转动副轴线方向

s_(A2) =T_1 s_(C2) =(-3/2,1/2-√2,-1/2-(√2)/2)

s_(B2) =T_1 s_(A2) =(-1/2-(√2)/2,-3/2,1/2-√2)

由于图1.1中六边形D1D2E1E2F1F2与A1A2C1C2B1B2不直接连接，且这两个六边形的结构是相同的，因此在六角边形D1D2E1E2F1F2设置相同的Bricard机构。利用三维对称性，2个六边形处的Bricard机构关于坐标原点对称，其中 s_(D1) ,s_(E1) ,s_(F1) 依然相交于坐标原点并分别指向各自对应顶点，则其各个顶点处转动关节的轴线可按照上述求解过程同理可得：

s_(D1) =(-√2,0,-(√2)/2)

s_(D2) =(3/2,1/2+(√2)/2,-1/2+√2)

s_(E1) =(-(√2)/2,-√2,0)

计算过程与说明 | 结果


4 整体系统的机构网格 到目前为止，为构造多面体连杆机构，已经求得两个相同的三重对称Bricard机构的转动轴线位置，如图1.4所示，除Bricard机构所含的转动关节（12个），其余顶点则暂时设置为球副。计算机模拟后，此可折展多面体具有两个自由度。进一步的，如图1.5所示，利用对称性，将A3 , B3 和C3处的球副替换转动副，可得到单自由度系统。 图1.4 包含两个Bricard机构的整体多面体构造 其中，与B1的轴线方位相似，A3处转动关节可平分∠A2A3E3并指向多面体中心，则杆A2A3与杆E3A3绕其转动后可重合。同理，A3，B3，C3处转动关节相交于坐标原点并分别指向各自对应顶点，则有 s_(A3) =(√2,-(√2)/2,0) s_(B3) =(0,√2,-(√2)/2) s_(C3) =(-(√2)/2,0,√2)

计算过程与说明 | 结果

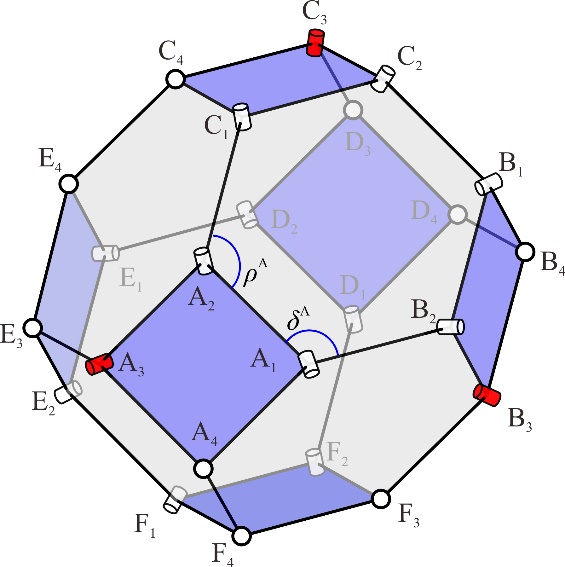
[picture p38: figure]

图1.5 A3 , B3 和C3处的转动副替换设计

二 可展多面体三维建模

在确定转动副空间位置后，接下来可在三维建模软件（如Solidworks）中模拟可展多面体的运动过程。以图1.2中六边形面 处的Bricard机构为例，首先初步选取多面体中正方形单元的边长为200mm，厚度可自行合理选取。其次，按照计算结果标明正方形单元和连接杆件的转动副空间位置，对转动副轴线依次进行重合配合，如下图所示构造其中一个Bricard机构。

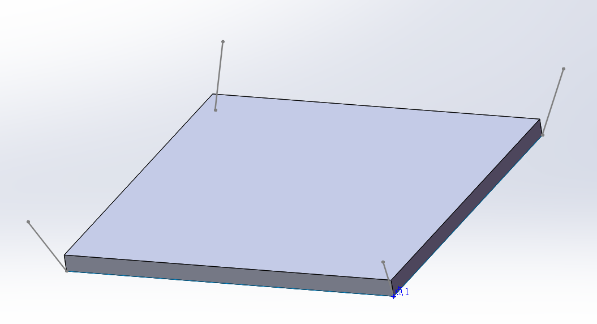
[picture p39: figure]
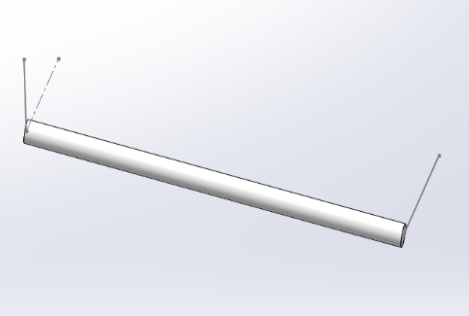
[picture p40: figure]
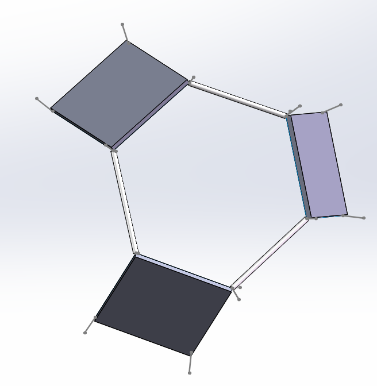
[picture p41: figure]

图2.1 六边形面 A_1 A_2 C_1 C_2 B_1 B_2 处Bricard机构建模

接着，利用已知的轴线位置，可用同样的方式对整个多面体进行初步建模。进一步的，用圆柱体来代表转动铰链，用球体代表球铰链，便可在多面体各个顶点配置已知空间位置的铰链。在三维软件组装完整的多面体装配体，可模拟出如下所示的运动顺序概念图。

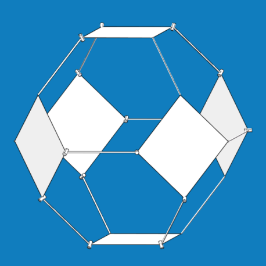
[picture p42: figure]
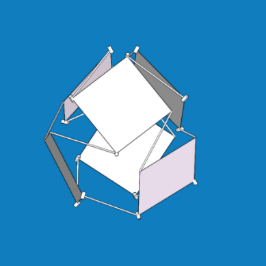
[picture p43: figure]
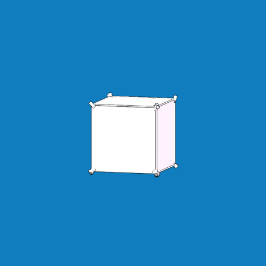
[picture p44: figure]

图2.2 可展多面体运动顺序概念图

三 原理样机搭建

除概念图外，为完成原理样机的构建，零件及铰链的具体物理形式还需进一步设计和优化。在保证运动副轴线位置不变的前提下，带铰链底座的正方形板及连接杆的具体物理实现形式如下图所示，以及由此构建其中一个Bricard机构。

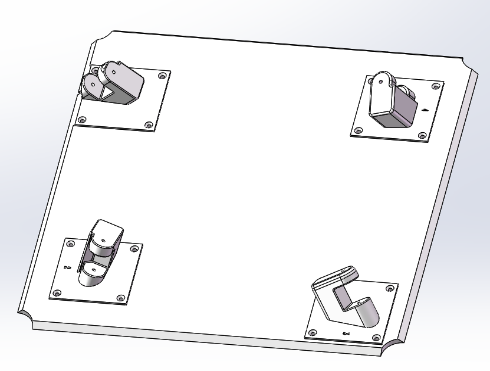
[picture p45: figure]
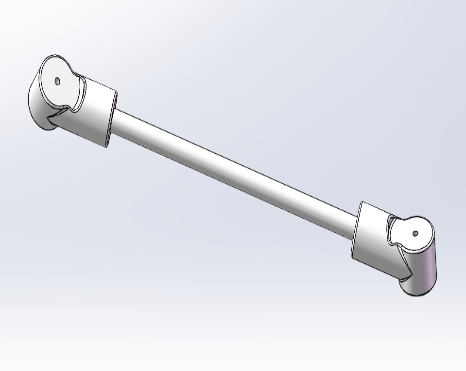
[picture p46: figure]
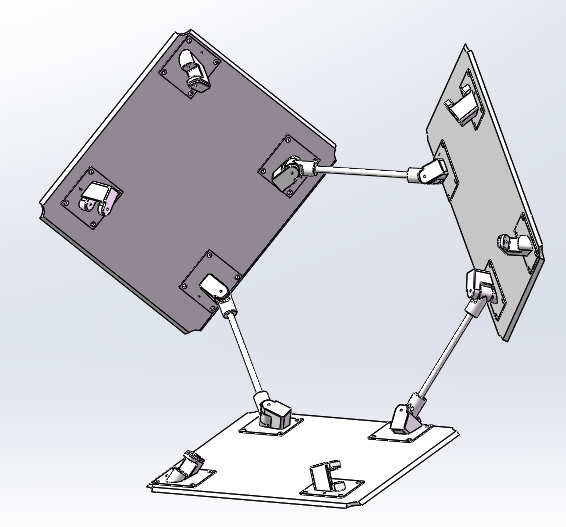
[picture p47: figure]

图3.1 零件设计优化与Bricard机构构建

同理，对各个所需零件进行优化设计以搭建完整的多面体结构。其中，对于一个球铰链，此处采用三个转动铰链来等效代替。因保留了各个转动副的空间位置坐标，多面体结构的折展运动未受影响。原理样机的搭建和运动顺序如下图所示，其中采用亚克力材料制作正方形面板，刚性杆件和连接铰链为3D打印制品或金属材料。

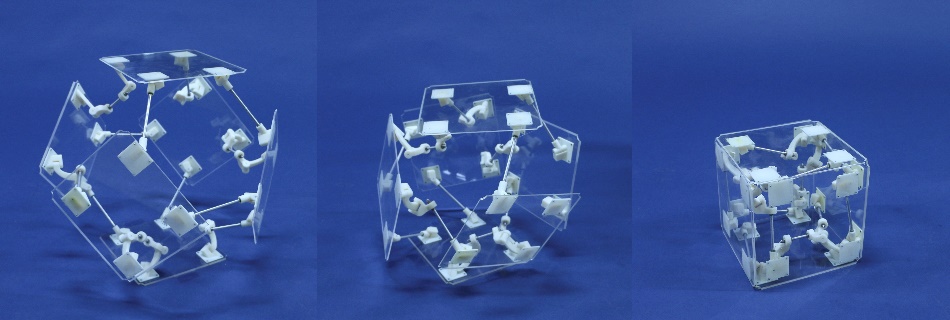
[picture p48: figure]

图3.2 可展多面体运动顺序概念图

所用零件清单如下：

零件类型 | 方形面板 | 铰链底座 | 直杆1 | 直杆2 | 直杆3
数量 | 6 | 24 | 6 | 6 | 3
零件类型 | 弯杆1 | 弯杆2 | 螺栓 | 轴承 | 圆柱销
数量 | 9 | 9 | 96 | 18 | 30

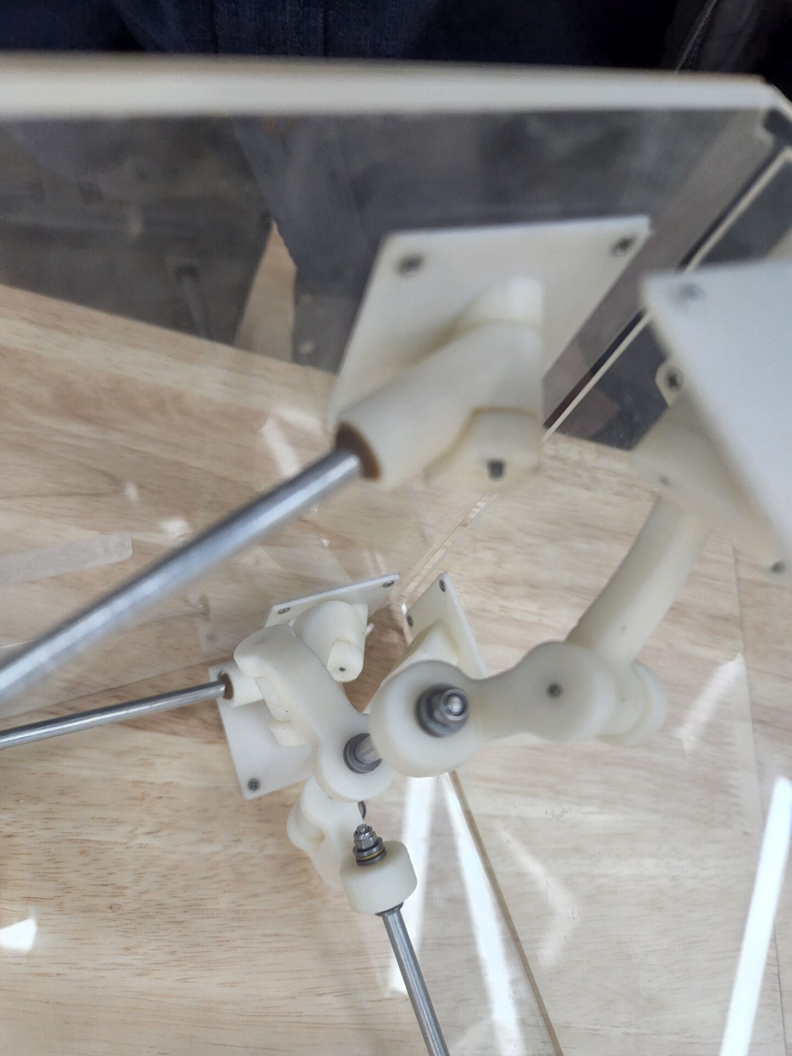
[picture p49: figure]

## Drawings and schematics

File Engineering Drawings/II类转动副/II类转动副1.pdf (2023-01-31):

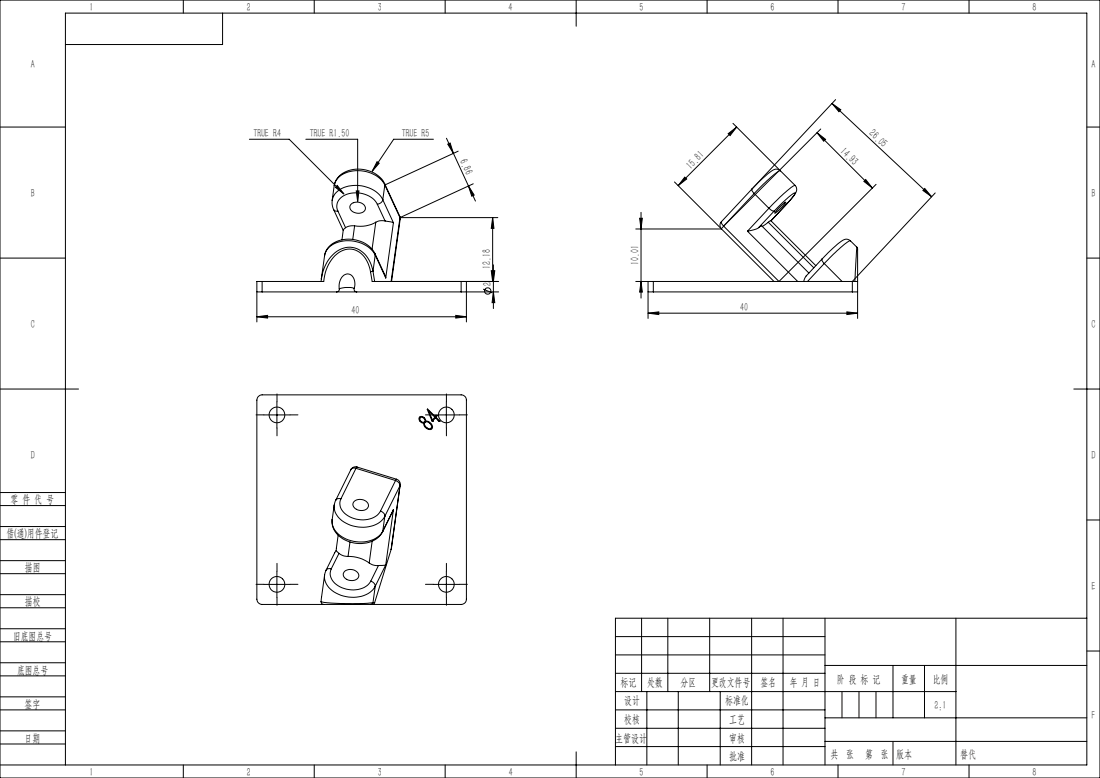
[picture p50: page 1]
TRUE R5; TRUE R4; TRUE R1.50

标记 | 处数 | 分区 | 更改文件号 | 签名 | 年 月 日
设计 | | | 标准化 | | | | | 2:1
校核 | | | 工艺
主管设计 | | | 审核

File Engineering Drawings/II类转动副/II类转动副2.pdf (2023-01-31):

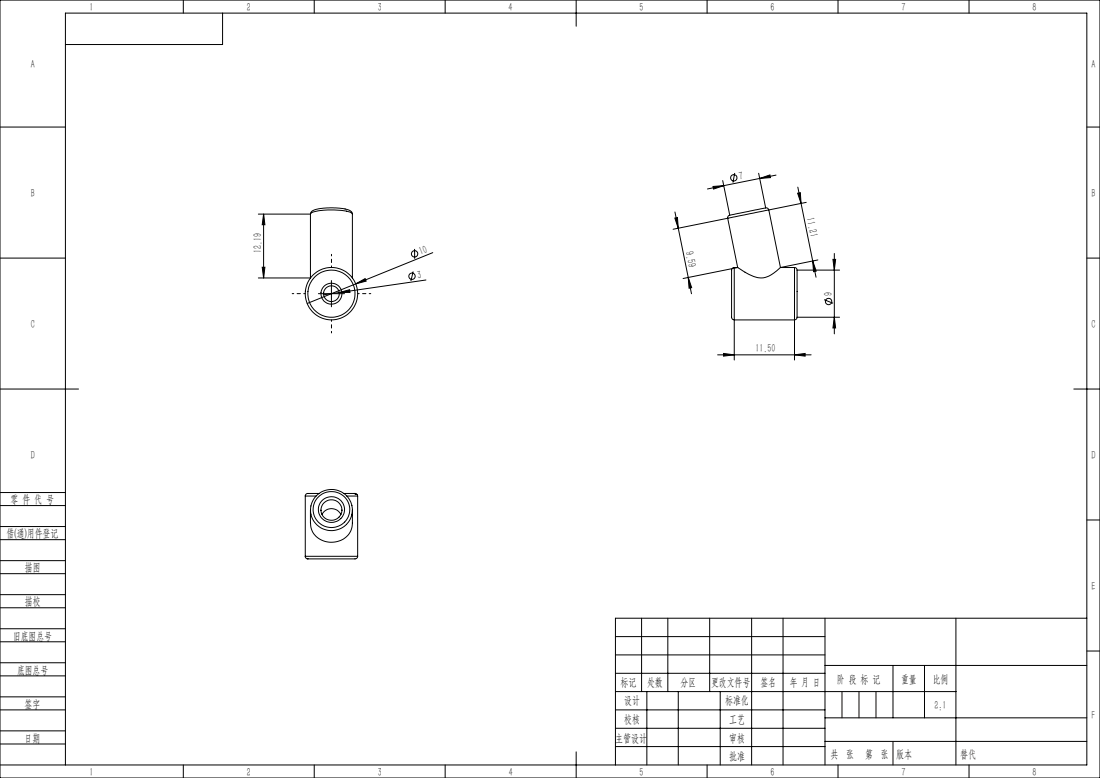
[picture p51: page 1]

标记 | 处数 | 分区 | 更改文件号 | 签名 | 年 月 日
设计 | | | 标准化 | | | | | 2:1
校核 | | | 工艺
主管设计 | | | 审核

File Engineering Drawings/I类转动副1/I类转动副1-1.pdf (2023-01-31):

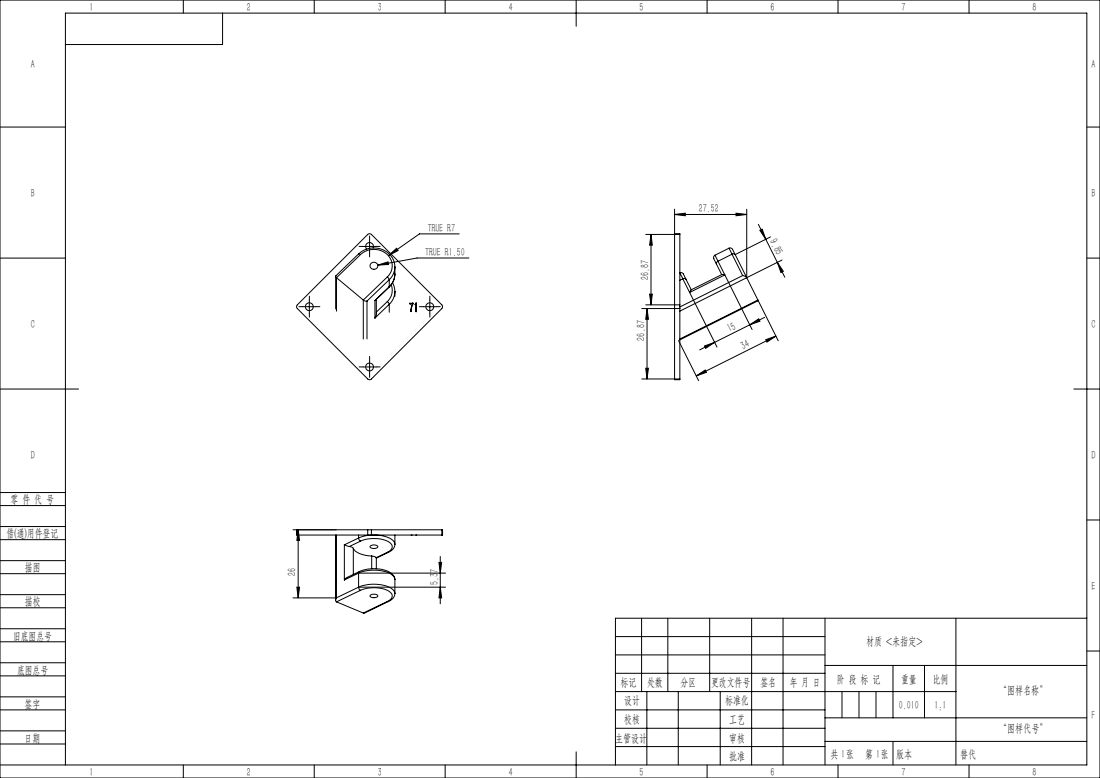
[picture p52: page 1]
TRUE R7; TRUE R1.50

材质 <未指定>

阶 段 标 记 | 重量 | 比例 | “图样名称”

标记 | 处数 | 分区 | 更改文件号 | 签名 | 年 月 日
设计 | | | 标准化 | | | | | 0.010 | 1:1
校核 | | | 工艺
主管设计 | | | 审核

“图样代号”

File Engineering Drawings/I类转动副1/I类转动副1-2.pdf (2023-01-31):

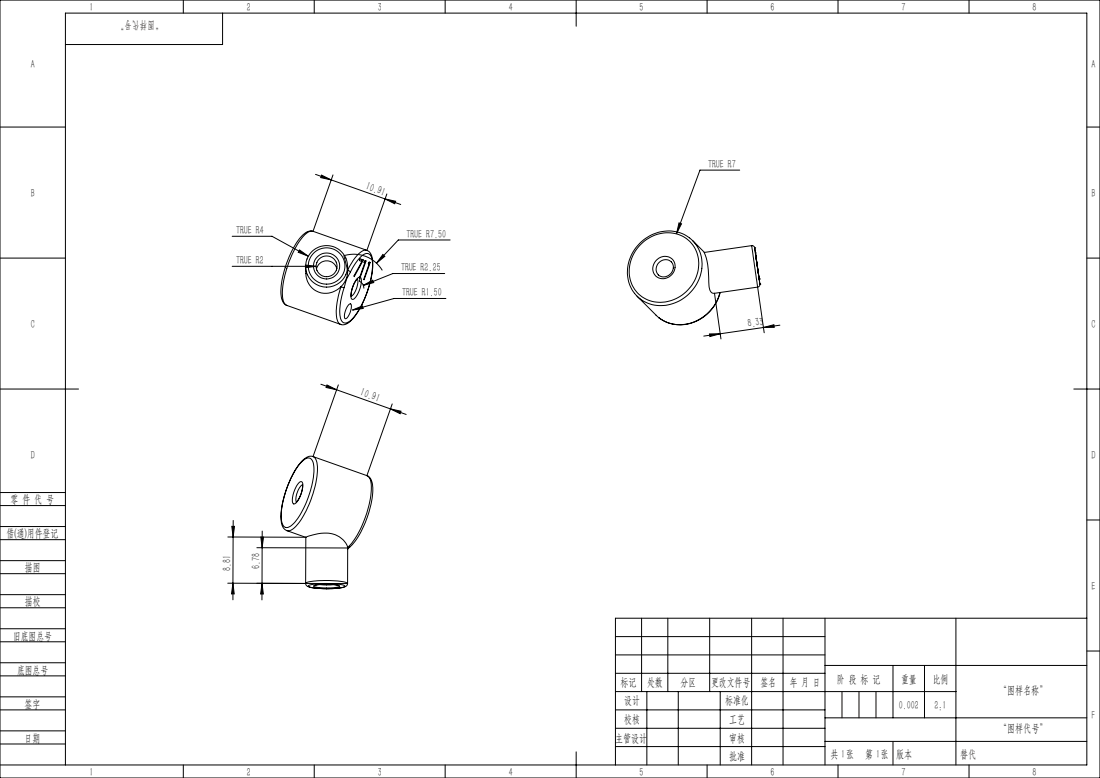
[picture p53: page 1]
TRUE R7.50; TRUE R2.25; TRUE R1.50; TRUE R2; TRUE R4; TRUE R7

阶 段 标 记 | 重量 | 比例 | “图样名称”

标记 | 处数 | 分区 | 更改文件号 | 签名 | 年 月 日
设计 | | | 标准化 | | | | | 0.002 | 2:1
校核 | | | 工艺
主管设计 | | | 审核

“图样代号”

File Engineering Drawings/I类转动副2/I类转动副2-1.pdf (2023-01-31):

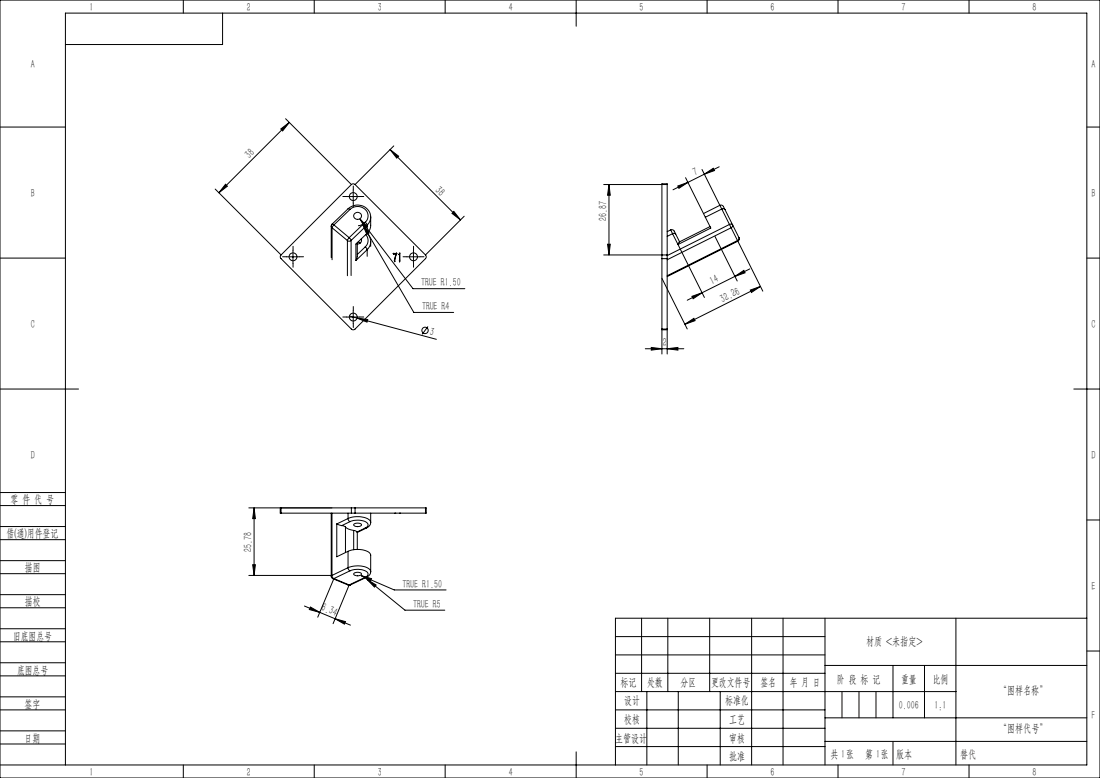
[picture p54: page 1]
TRUE R4; TRUE R1.50 3; TRUE R1.50; TRUE R5

材质 <未指定>

阶 段 标 记 | 重量 | 比例 | “图样名称”

标记 | 处数 | 分区 | 更改文件号 | 签名 | 年 月 日
设计 | | | 标准化 | | | | | 0.006 | 1:1
校核 | | | 工艺
主管设计 | | | 审核

“图样代号”

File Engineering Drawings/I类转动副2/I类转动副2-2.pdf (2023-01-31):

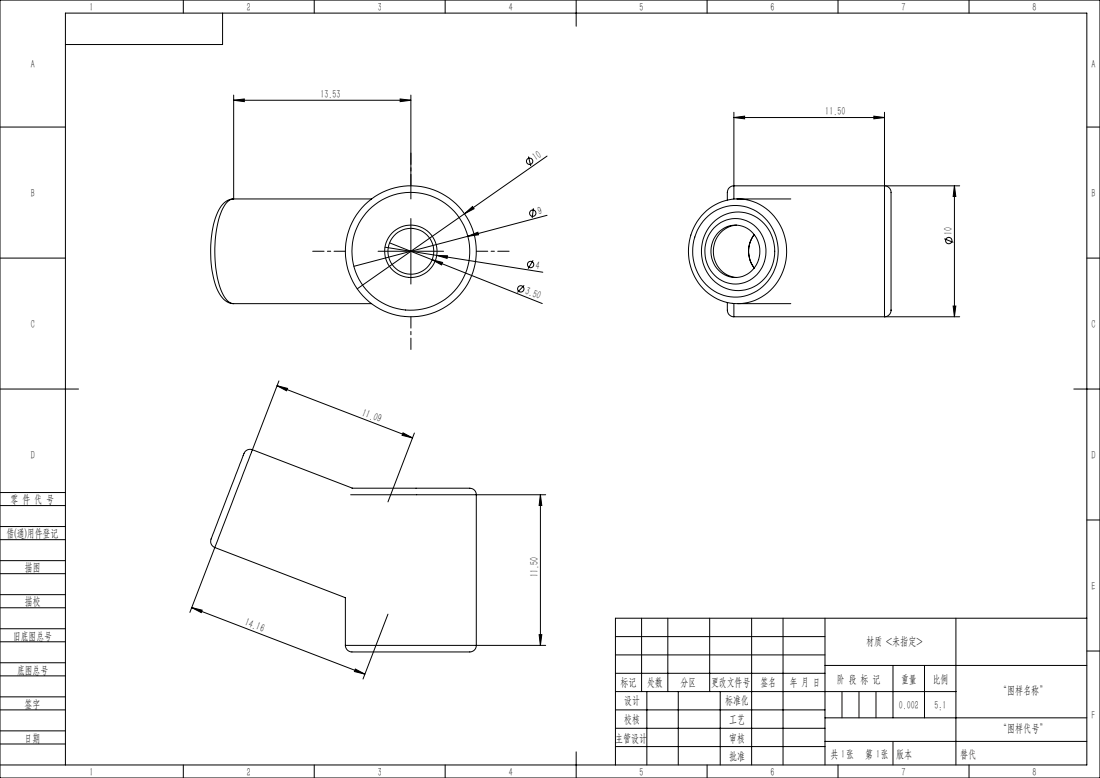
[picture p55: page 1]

材质 <未指定>

阶 段 标 记 | 重量 | 比例 | “图样名称”

标记 | 处数 | 分区 | 更改文件号 | 签名 | 年 月 日
设计 | | | 标准化 | | | | | 0.002 | 5:1
校核 | | | 工艺
主管设计 | | | 审核

“图样代号”

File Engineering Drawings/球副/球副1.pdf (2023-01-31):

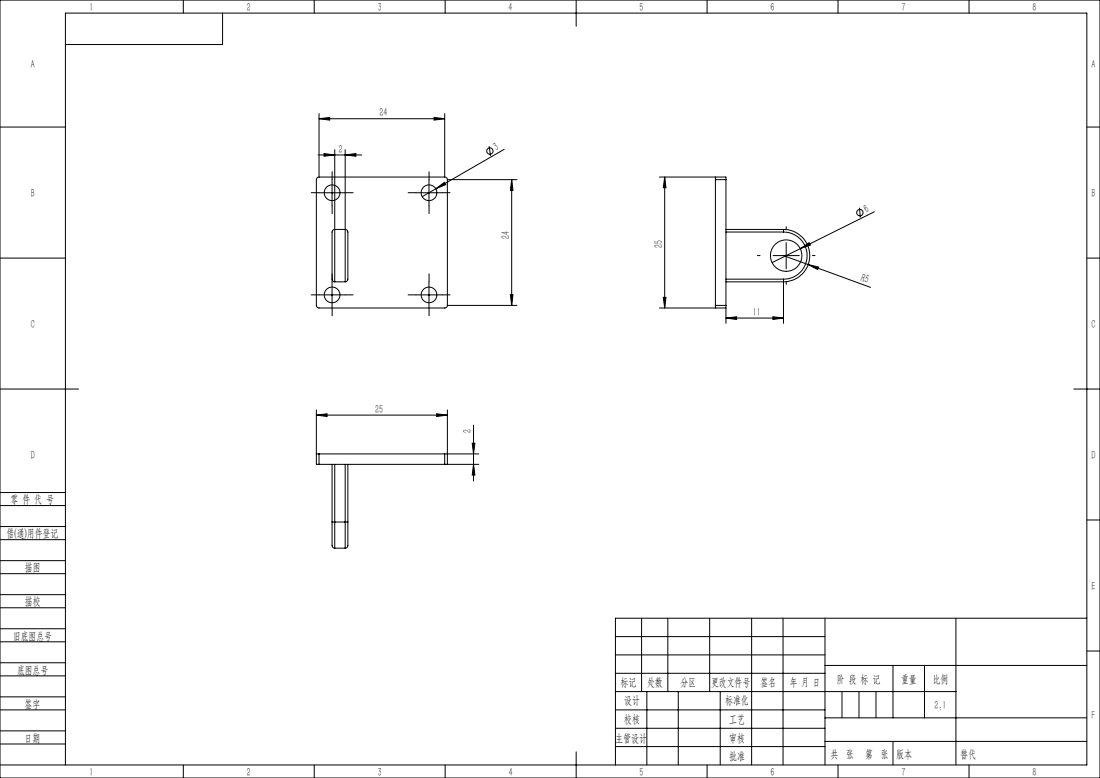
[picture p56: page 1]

标记 | 处数 | 分区 | 更改文件号 | 签名 | 年 月 日
设计 | | | 标准化 | | | | | 2:1
校核 | | | 工艺
主管设计 | | | 审核

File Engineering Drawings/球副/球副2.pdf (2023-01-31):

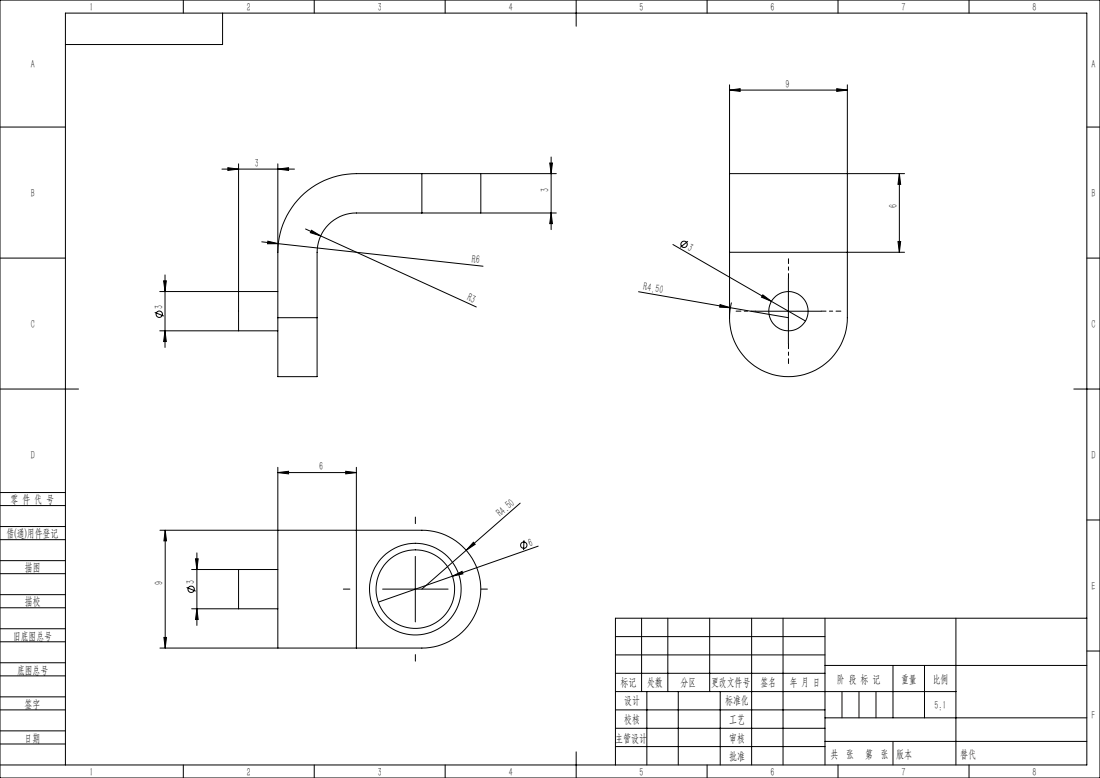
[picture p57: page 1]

标记 | 处数 | 分区 | 更改文件号 | 签名 | 年 月 日
设计 | | | 标准化 | | | | | 5:1
校核 | | | 工艺
主管设计 | | | 审核

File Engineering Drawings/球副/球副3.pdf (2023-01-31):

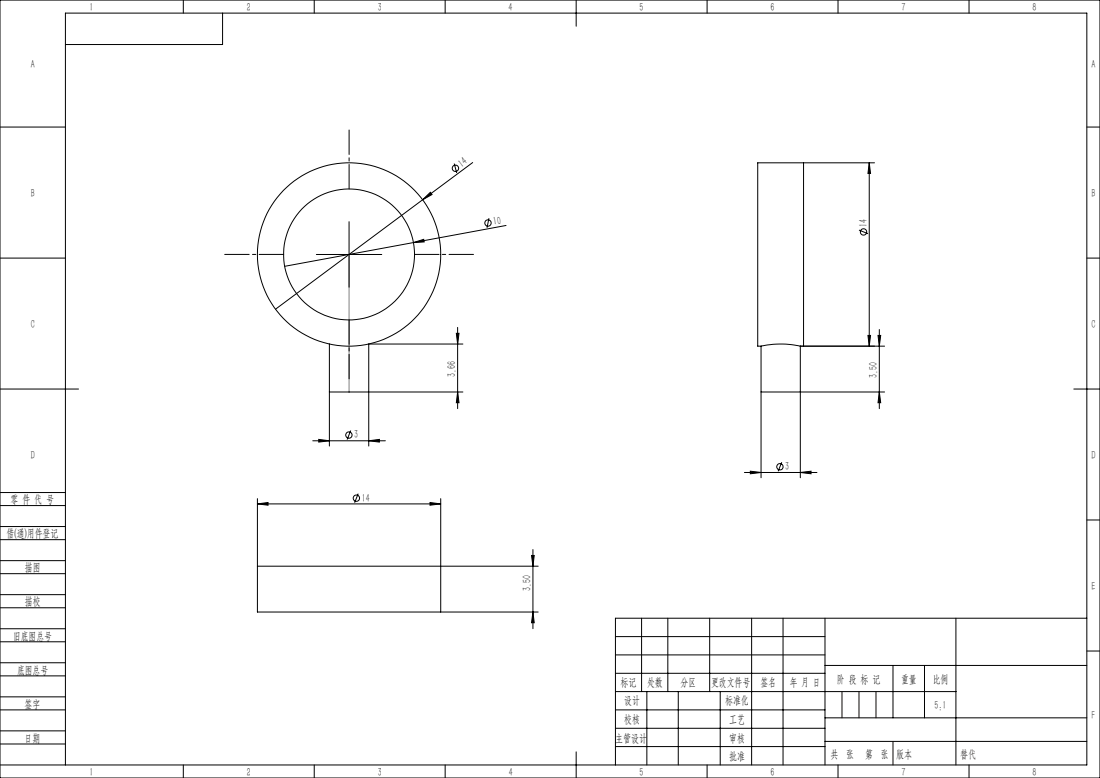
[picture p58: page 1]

标记 | 处数 | 分区 | 更改文件号 | 签名 | 年 月 日
设计 | | | 标准化 | | | | | 5:1
校核 | | | 工艺
主管设计 | | | 审核

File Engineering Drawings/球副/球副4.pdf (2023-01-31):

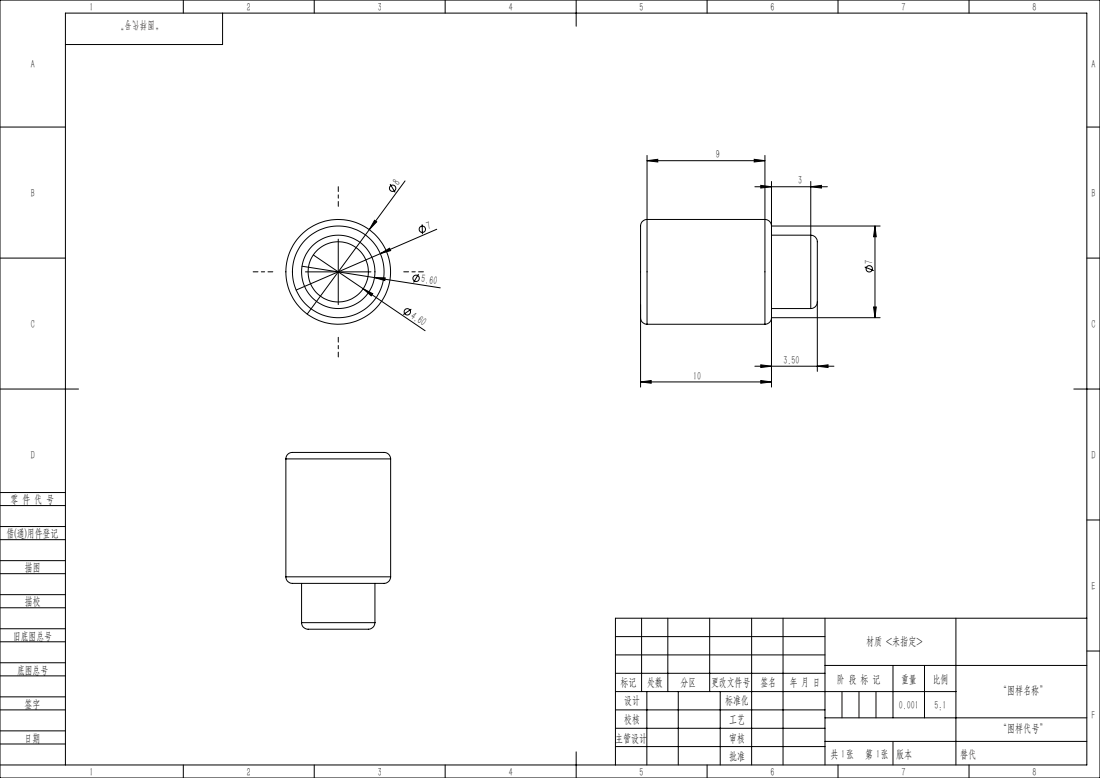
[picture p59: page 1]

材质 <未指定>

阶 段 标 记 | 重量 | 比例 | “图样名称”

标记 | 处数 | 分区 | 更改文件号 | 签名 | 年 月 日
设计 | | | 标准化 | | | | | 0.001 | 5:1
校核 | | | 工艺
主管设计 | | | 审核

“图样代号”
